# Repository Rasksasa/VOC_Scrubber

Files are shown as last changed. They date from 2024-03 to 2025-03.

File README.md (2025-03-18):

# VOC Scrubber
A Volatile Organic Compound filter made to remove 3D printing fumes where they are most likely to be efficiently.

## Introduction

If you are like me and had a chance (and a rather stupid one) of sticking your head above the print bed while the printer is running; two things will hit you - heat from the rising air and fumes from the print. Almost all current printer filters, open source or commercial, does the same thing however; they are designed to be located near the print bed pulling air from the bottom. However when printing, the hot surface of the bed causes convective air currents to raise from the bed, up and back down the slides of the wall of the printer again (back to simple school level physics). You can see these vapour rise when pushing “wet” filament out a hot nozzle. So it is rather odd that almost all air filters are designed with the filters drawing air in from the lowest point in the print area/chamber. 

This “VOC Scrubber” is intended to address just that problem by filtering hot “dirty” air where they are most likely to go; at the top of the enclosed print space. The "VOC Scrubber" design objectives are: 

- Large(r) quantity of carbon pallet to give longer mean-time-between-service of the filter. In this case around 850ml of carbon pallets. 
- Intentional  use of slow air speed to maximise collision of VOC particles with the carbon pallets in combination with filter media depth to ensure high VOC removal in a single pass.
- 5015 blower fans to minimise the filter size while having generally higher pressure differential to pull air in efficiently across the carbon pallets and HEPA (surprisingly pulls a lot of air through too).
- Easy to source generic 40x105mm HEPA filter available from AliE to filter larger particles
- Direct and linear air paths (no vanes or right angles) allowing for maximum air flow with minimal pressure drops.

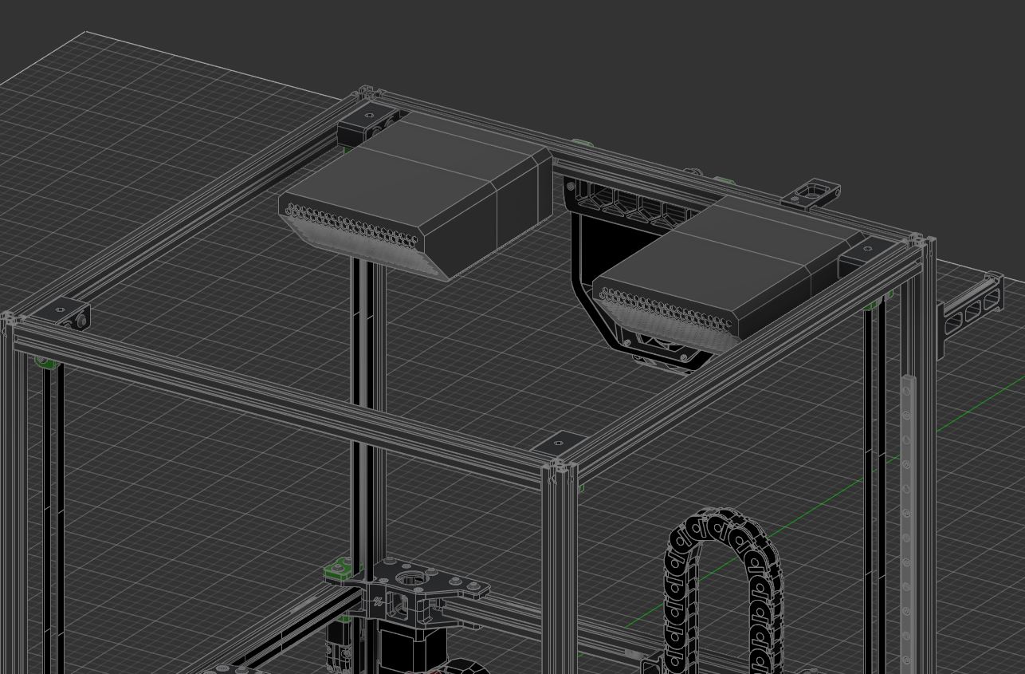
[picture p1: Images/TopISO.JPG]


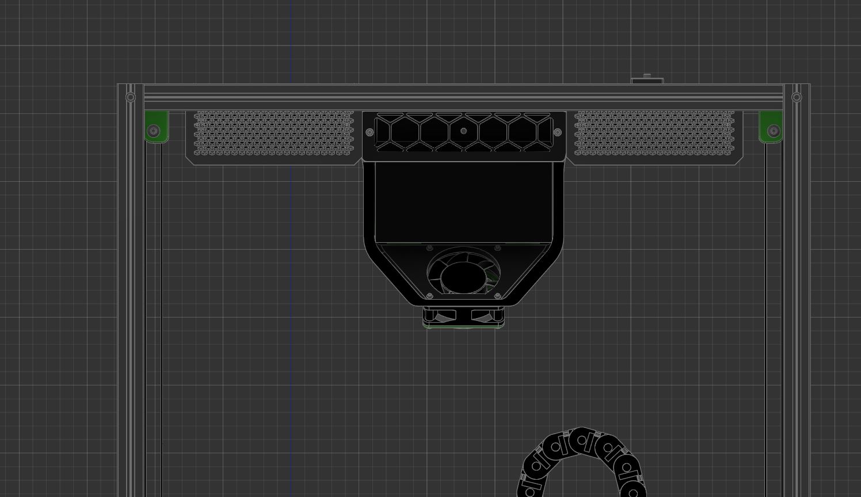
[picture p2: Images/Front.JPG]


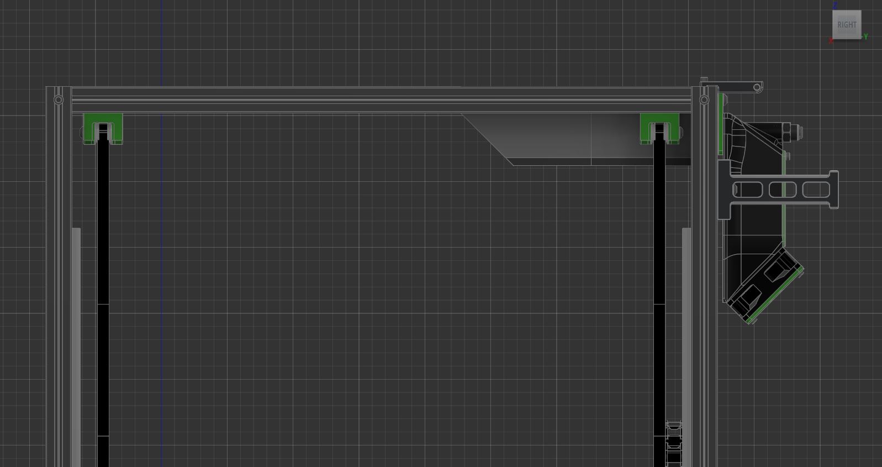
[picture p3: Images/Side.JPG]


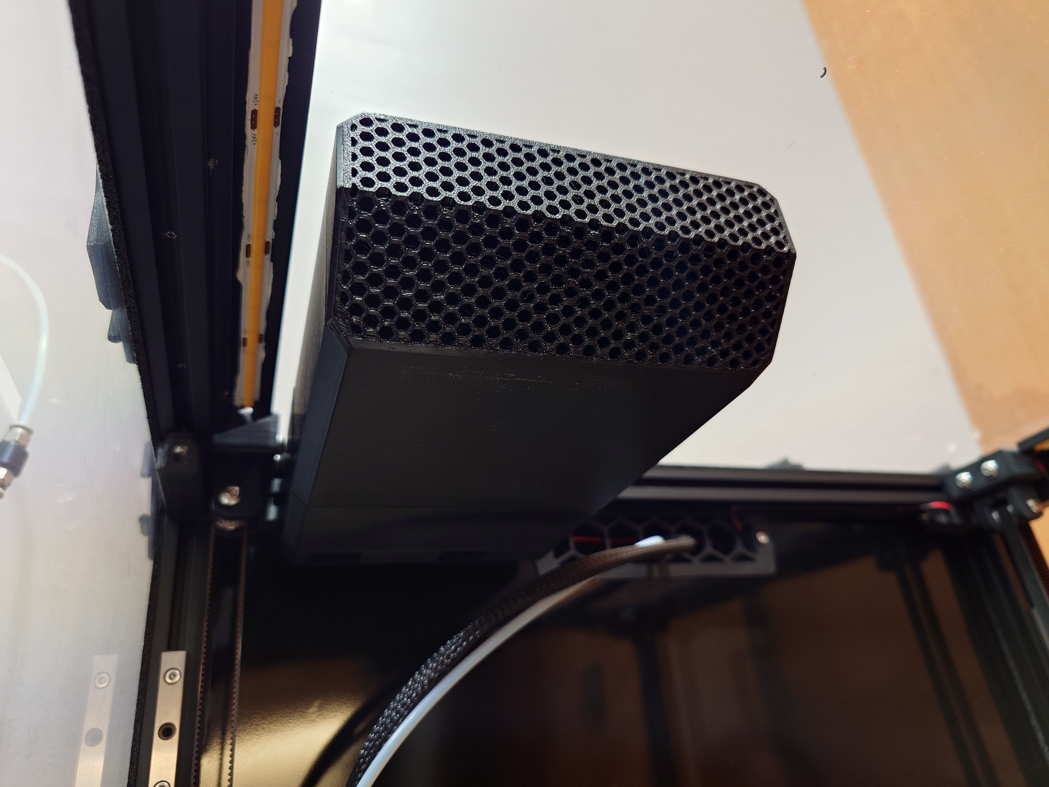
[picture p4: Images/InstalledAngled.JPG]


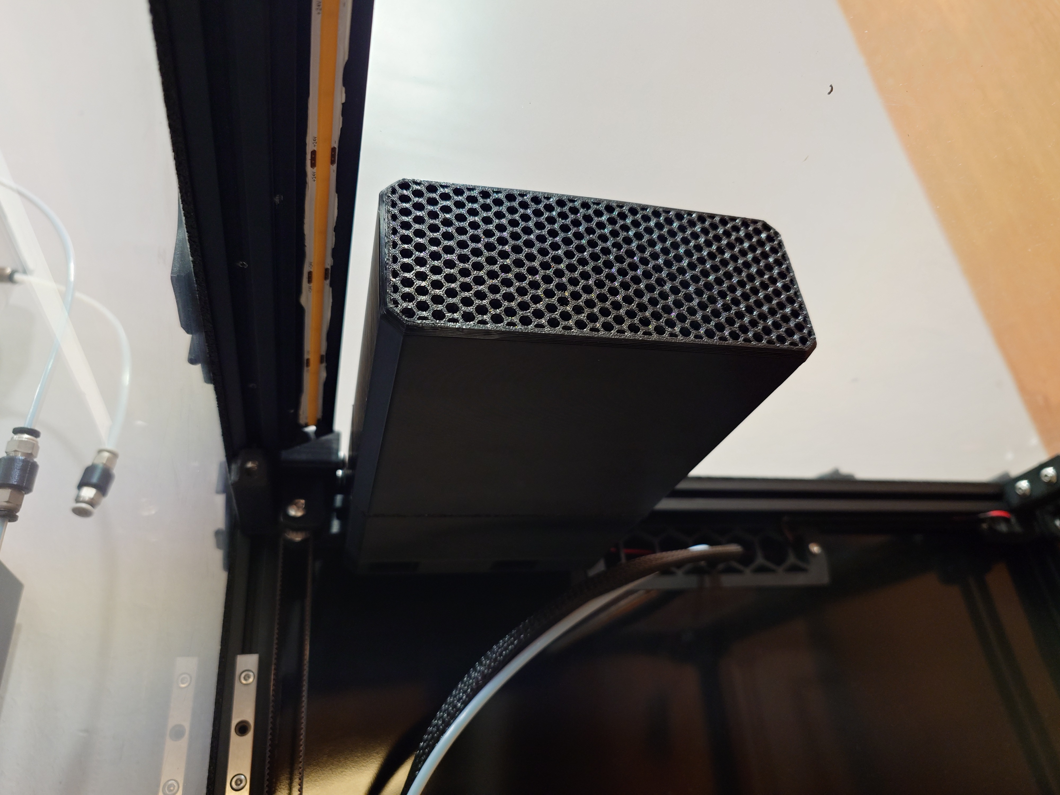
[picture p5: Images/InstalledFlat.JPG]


The VOC Scrubber has been designed with the Voron v2.4 350mm in mind but should fit any similarly designed 3D printers as long as there is an aluminium profile for it to be attached to. However it may only be possible to install 1 unit in a v2.4 250mm due to space constrains. 

## Bonus!

It looks like it would fit Voron Tridents too! I unfortunately do not have a Trident but it looks to fit just fine. 

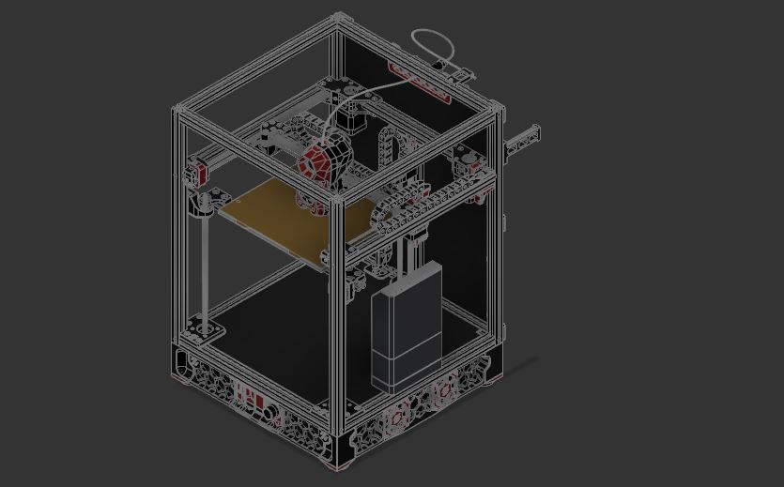
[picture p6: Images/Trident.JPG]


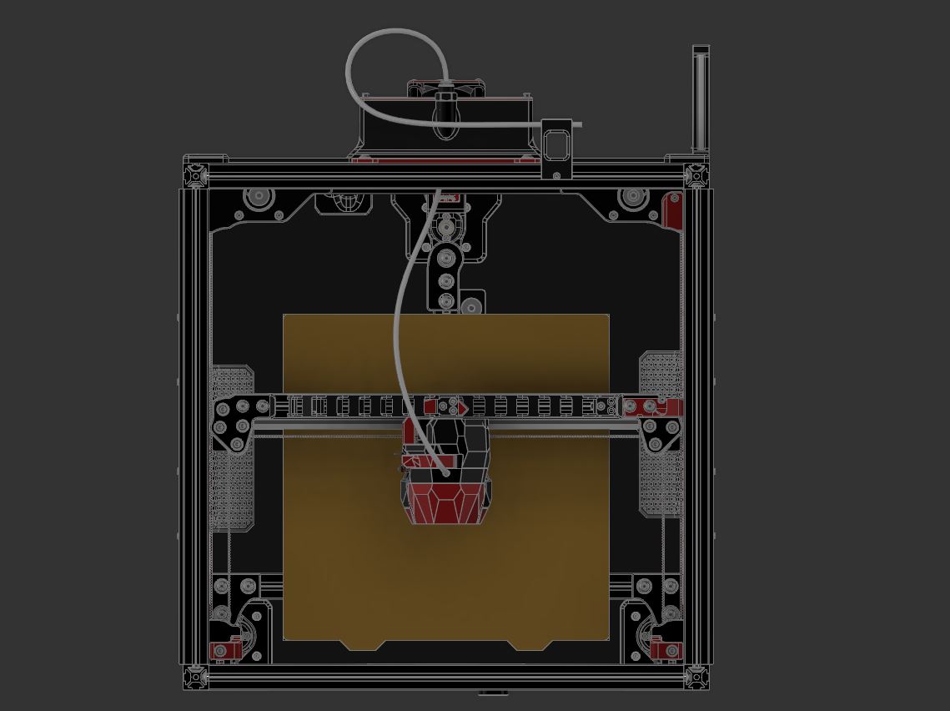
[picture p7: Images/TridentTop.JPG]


## BOM 

Required (Per unit VOC Scrubber) 

- 2x 5015 fans
- 10x 6x3mm (diameter x thickness) neodymium magnets (N54 rated magnets recommended)
- 7x M3x5x4mm “standard” Voron heatset inserts
- 2x M3x15mm SHCB
- 5x M3 roll-in T-nut
- 3x M3x30mm SHCS
- 2x M3x25mm SHCS
- 1x M3x20mm SHCS
- 2x M3x8mm FHCS
- 4x M3x8mm SHCS
- 1x HEPA Filter (40x105x12mm) (there are multiple sources on Aliexpress and some due to measuring errors may say 37x104mm sample: [https://www.aliexpress.us/item/3256801274573326.html](https://www.aliexpress.us/item/3256801274573326.html))

Consumables 

- Superglue for magnet installation

## Build & Install Guide
Refer to the CADs for a better idea about the installation.  

1. Printing is straight forward. Use standard Voron printing parameters in ABS or ASA. The only real decision you will need to make is between the Flat or Angled Cartridge design.
2. Install heatsets into the "Fan Cowling" printed part
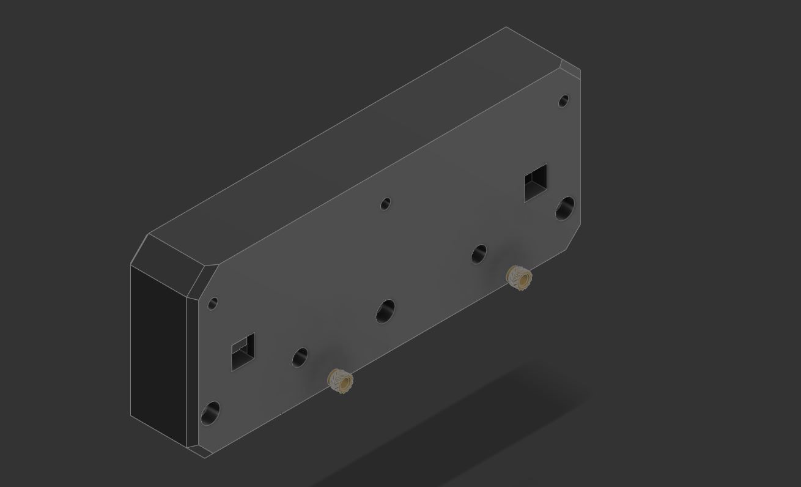
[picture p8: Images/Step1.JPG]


3. Intall heatset into the "Fan Hood" printed part (2 on the lower portion next to the walls in yellow). These are very tricky to install, but if you hold your soldering iron at an angle you will be able to catch the heatsets and slowly push it into position. Install magnets (in black) - dont forget to check the polarity.
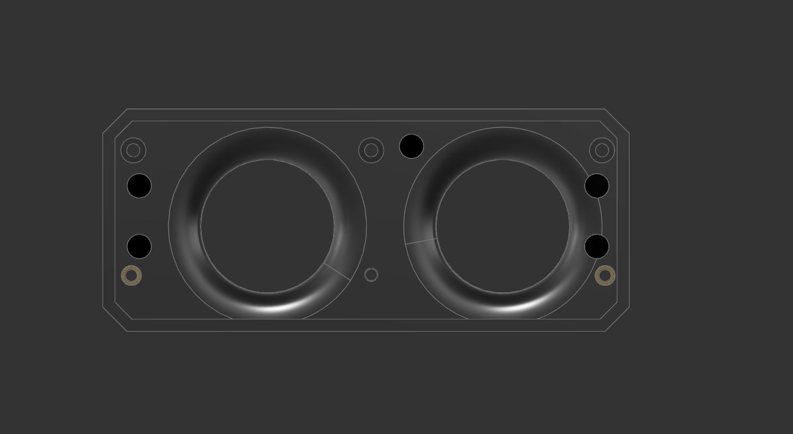
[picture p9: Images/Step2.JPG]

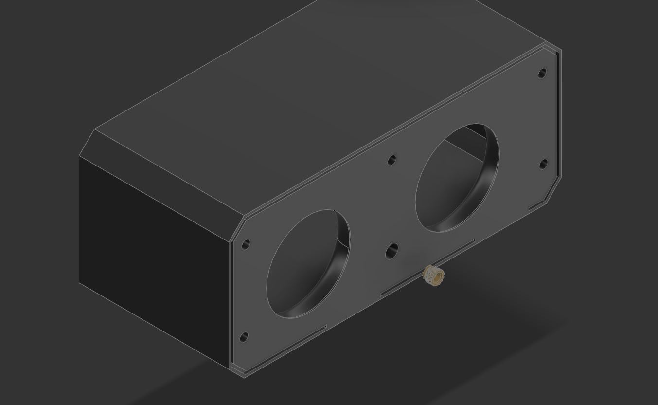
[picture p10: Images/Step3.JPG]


4. Decide which side of your printer you are installing and where the wires will run out from. The "Fan Cowling" has two exit holes to choose from. Wire the fans in parallel. The fans are fit in place for GDSTime fans, but if it is too lose just use some foam tape to fill out the gap as long as it secures the fan. 
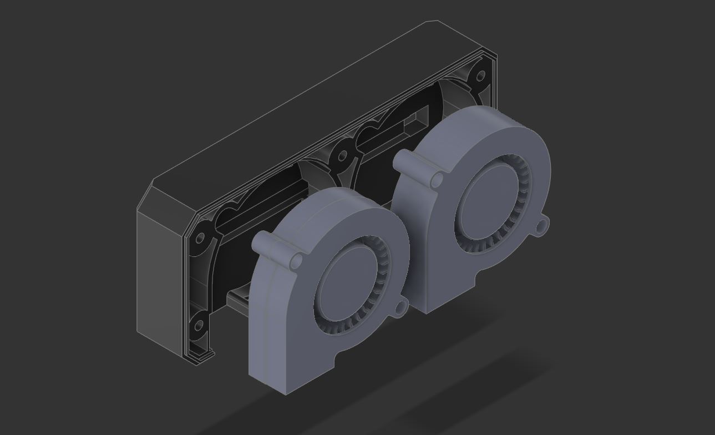
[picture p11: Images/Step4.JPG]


5. Once you have tested that the fans are working when powered, join the "Fan Cowling" and "Fan Hood" and screw from the back of the "Fan Cowling" using 2x M3x25mm SHCS on the sides and 1x M3x20mm SHCS at the middle.
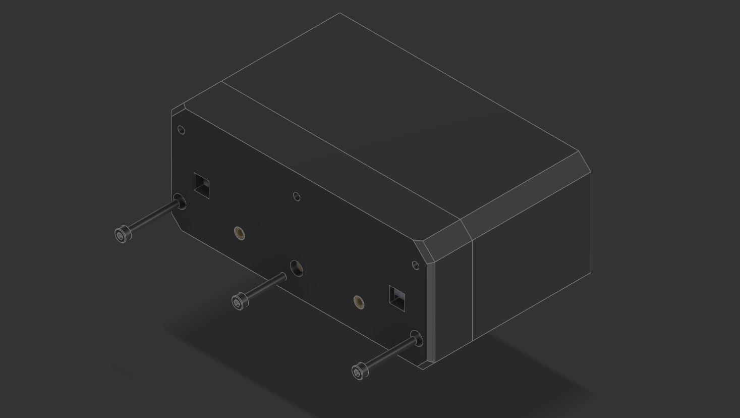
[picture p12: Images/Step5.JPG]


6. Attach the assembly to the 2020 frame using roll-in T-Nuts or Hammer T-Nuts and 3x M3x30mm SHCS. Run your cables and connect accordingly and test again to make sure they still work. 
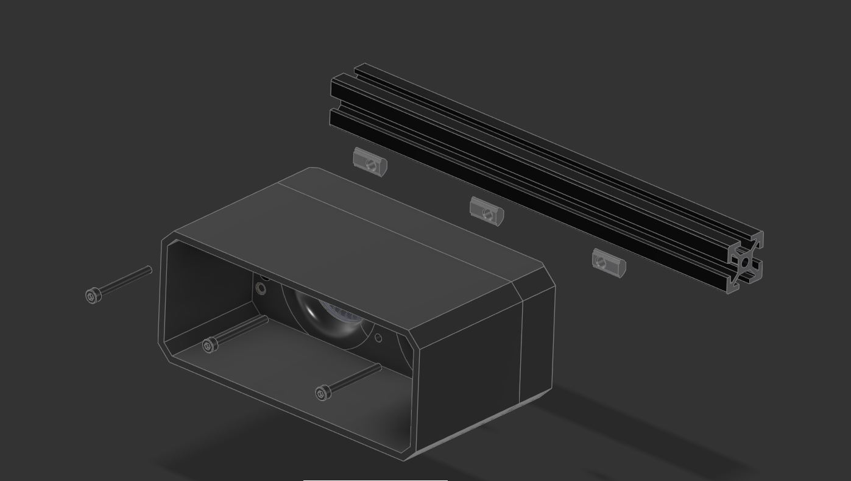
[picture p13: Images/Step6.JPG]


6a. (Optional) Install the "Frame Brace" using 4x M3x8mm SHCS. It may take some time to align them as you will be installing them from 2 different planes. I mark this as optional as I personally have been running my VOC Scrubbers without them and have no issues in stability. 
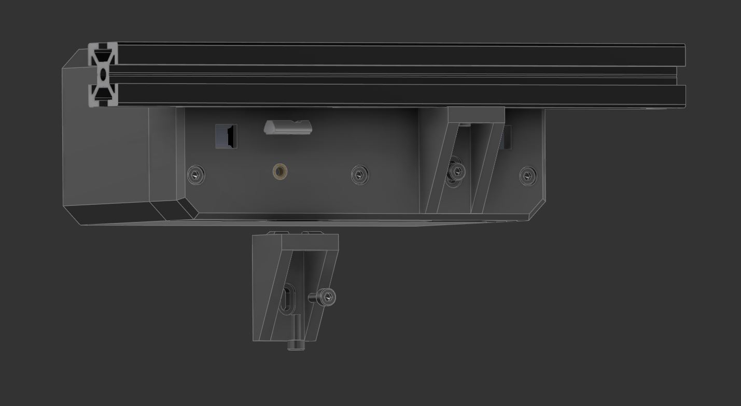
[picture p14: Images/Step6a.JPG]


7. Assemble the cartridge with heatsets. Install the magnets (in black - CHECK THE POLARITY BEFORE INSTALLING), install the HEPA filter, fill with activated carbon pallets and cover it with 2x M3x8mm FHCS. 
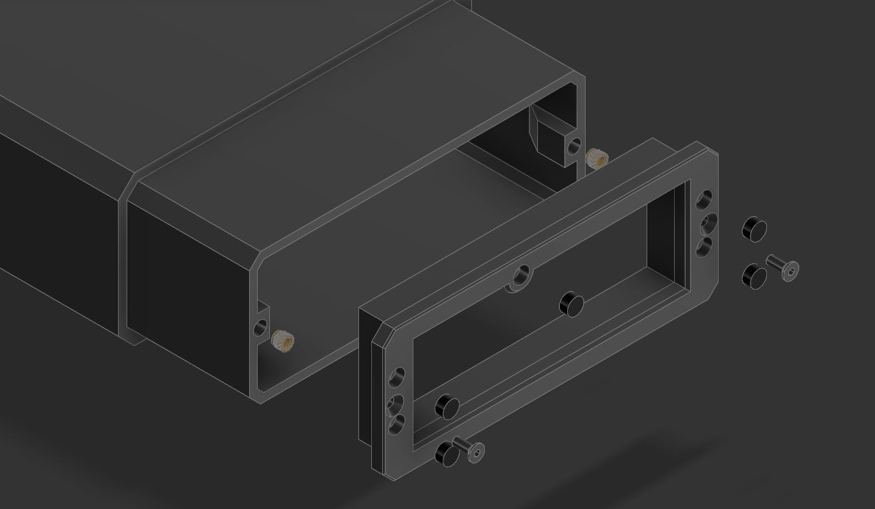
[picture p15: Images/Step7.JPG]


8. The cartridge should slide into the "Fan Hood" and held in place by the magnets. The whole assemble should also not wobble.
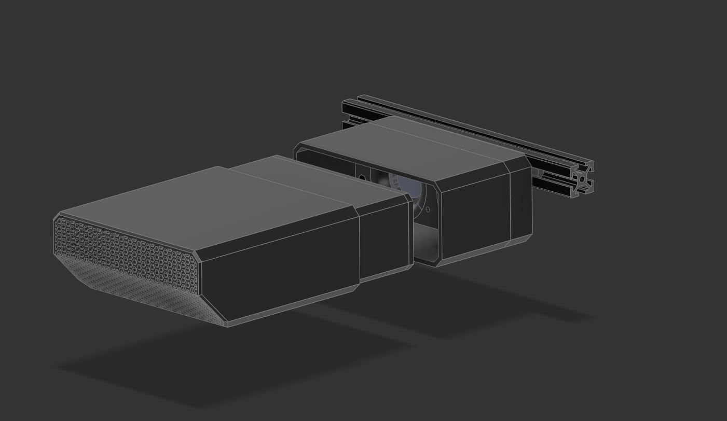
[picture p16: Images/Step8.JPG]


## Config & Macro(?)
I do not actually use any macros to actively control my fans. Rather my pre-heat macros just turns on the fans at 50%, and Print_Start turns it down to about 30% throughout the print job. 

## Notes:
There are two carbon pallet cartridge options and for all intent and purposes, achieve the same purpose. The Cartridge (Flat) option is easier and slightly faster to print while the Cartridge (Angled) was for a more aesthetic look at the risk of it being a harder print. Either is fine and holds roughly the same amount of carbon. 

I have been using it for the past month, and so far I have been very pleased with it. With this I have 3 methods for which I am controlling printing fumes:
1. [The Filter](https://github.com/nateb16/VoronUsers/tree/master/printer_mods/nateb16/THE_FILTER) which has been great to filter VOC will now focus on chamber heating by means of reduced carbon pallets
2. [VEFACH](https://github.com/VoronDesign/VoronUsers/tree/main/printer_mods/KevinAkaSam/VEFACH) will provide negative air pressure to ensure leakages are minimised through leaks.
3. Finally VOC Scrubber will be used as the main VOC remover in the chamber. 

The build chamber still needs to be sufficiently well sealed to ensure gases do not leak. Currently I can run my VEFACH at 15% and have absolutely no ordour in the room. The only problem I foresee with this mod is the potential loss in print height, but since I almost never print anything taller than 200mm I will probably never know. Fact is, printing the carbon pallet cartridges from this mod is the tallest I ever needed to in my 2.4. 

# Update Log 

## v1.2 (Mar 2025)
- Corrected some minor tolerance issues on the Cartridge cover for the FHCS and made the cover just slightly thinner (0.5mm) for clearance issue.
- Got rid of the Foam insert on the Cartridge to make it easier to build with less parts. 

## v1.1 (Feb 2025)
- Decided to position the air sensors at the exhaust VOC filter which I am in the process of designing hence the sensor on the Scrubber is mooted - removed internal sensor placement and wiring pass throughs.
- Increased clearance in the Fan Hood between the cartridge and 5015 fans by 1.5(?)mm.
- Reworked existing wiring pass through of the Fan Cowling for a cleaner design.
- Other aesthetic cleanups with no performance impact.

## v1.0 (Dec 2024)
- Complete ground up redesign of the filter as the changes being made were quite substantial 
- Implemented spacing for foam tape at key areas suspected to be susceptible to leaking air
- Shorter by 5mm by making the whole design flush to the height of a 5015 fan and the fan cowling integral with the hood

## Release for Review (Apr 2024)
- Release candidate to gather feedback on overall design and approach

## To do & Wishlist:
- Different HEPA filter that is even easier to source as I notice it being harder to source 40x105mm filters compared to when I first started using them

- ~~Validate print settings for the parts (i.e. if standard Voron print settings are sufficient)~~
- ~~Investigate VOC sensor options (i.e. SGP40 or ENS160)~~ 
- ~~Slots for 1mm thick foam tape where required to keep air from leaking/lost of pressure~~
- ~~Validate overall fit & finish especially for the VOC sensor + connector type/size to be used~~
- ~~Validate that 4 pairs of magnets are sufficient to hold the carbon pallet canister in place~~
- ~~Investigate impact on input shaping~~
- ~~"Slim" version to minimise print height loss~~

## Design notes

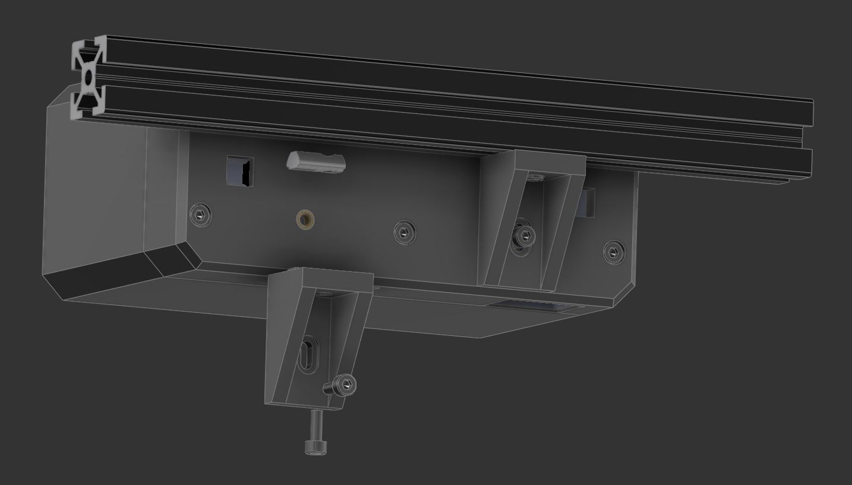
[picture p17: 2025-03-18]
Images/Capture6a.JPG

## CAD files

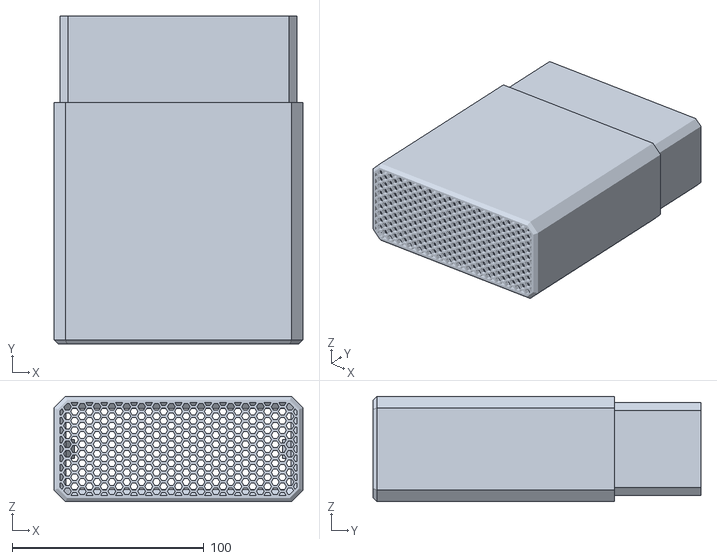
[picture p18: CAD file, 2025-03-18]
STL/Cartridge Flat (Option 2).stl
130.0 x 171.0 x 55.0

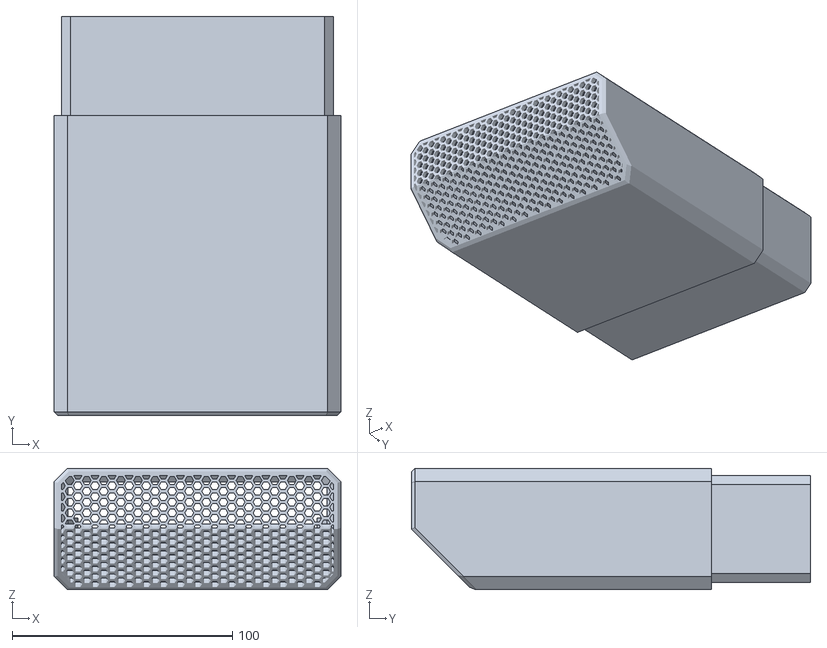
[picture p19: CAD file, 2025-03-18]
STL/Cartridge Angled (Option 1).stl
130.0 x 181.0 x 55.0

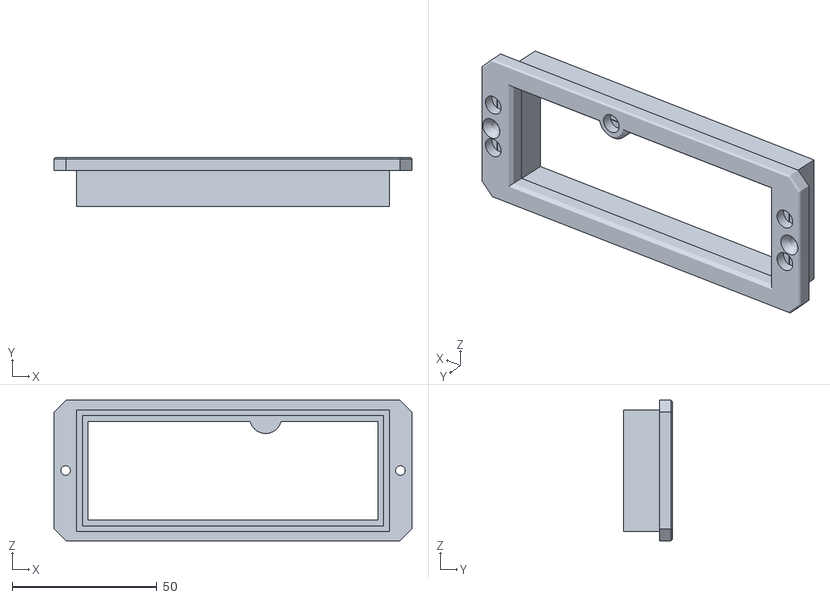
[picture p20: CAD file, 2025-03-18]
STL/Cartridge Cover.stl
123.5 x 17.0 x 48.5

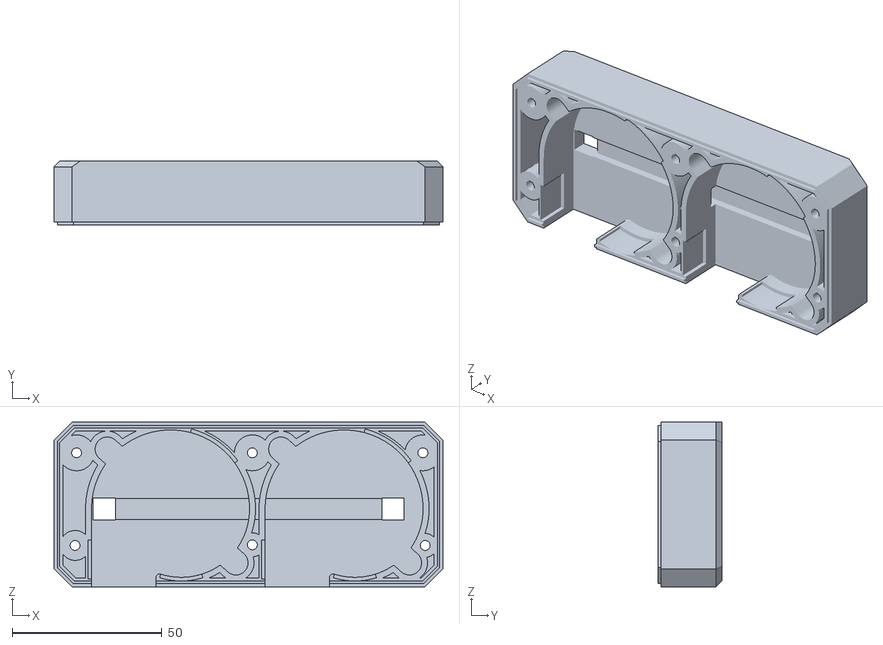
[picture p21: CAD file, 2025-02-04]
STL/Fan Cowling.stl
130.0 x 21.5 x 55.0

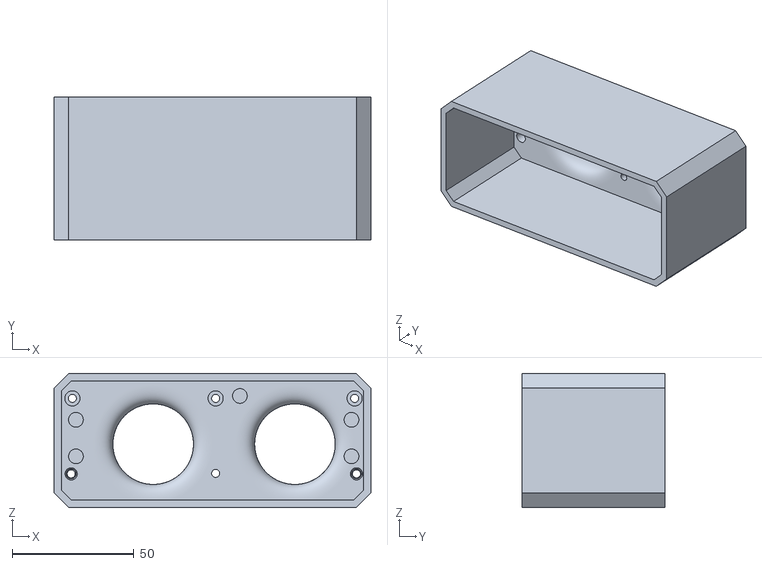
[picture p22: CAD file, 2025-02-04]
STL/Fan Hood.stl
130.0 x 58.5 x 55.0

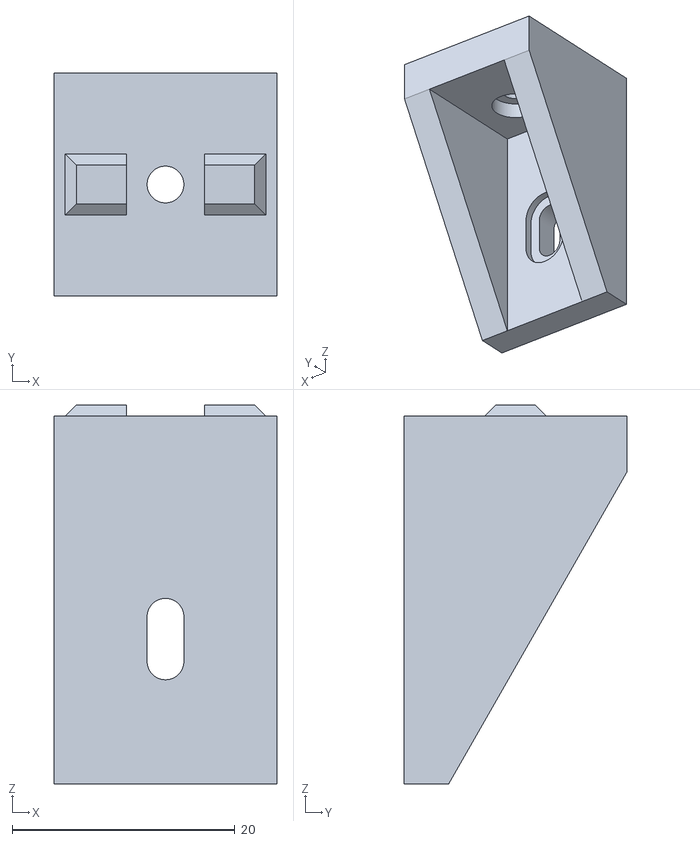
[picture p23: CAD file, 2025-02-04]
STL/2020 Profile Bracket x2.stl
20.0 x 20.0 x 34.0

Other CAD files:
CAD/VOC Scrubber v1.2.f3d

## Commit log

2024-03-08 Create CAD
2025-01-17 v1.0
    Initial release
    [2020 Profile Bracket x2.stl, Cartridge Angled (Option 1).stl, Cartridge Cover.stl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]
2025-01-17 Create Cartridge Flat (Option 2).stl
    [Cartridge Flat (Option 2).stl]
2025-01-17 Minor fixes to the Angled Cartridge
    [Cartridge Angled (Option 1).stl, VOC Scrubber v1.0.f3d]
2025-02-04 v1.1 Update
    [2020 Profile Bracket x2.stl, Cartridge Angled (Option 1).stl, Cartridge Cover.stl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]
2025-02-13 Minor fix to tolerances
    Fixed the 6x3mm magnet holes on the cartridge cover by 0.25mm deeper.
    [Cartridge Cover.stl, VOC Scrubber v1.1.f3d, VOC Scrubber v1.2.f3d]
2025-03-18 Update to v1.2
    Refer to the Readme for details.
    [Cartridge Angled (Option 1).stl, Cartridge Cover.stl]
2025-03-18 Re-upload STL
    [2020 Profile Bracket x2.stl, Cartridge Angled (Option 1).stl, Cartridge Cover.stl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]
